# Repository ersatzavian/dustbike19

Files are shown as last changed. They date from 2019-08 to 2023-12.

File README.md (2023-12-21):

# Dustbike 2019

Project to put some custom lights on my crappy playa bike. 

## Key Parts

Part | Manufacturer | Manufacturer Part Number | Qty| Link 
-----|--------------|--------------------------|----|------
Controller | ST Micro | Nucleo-L432KC | 1 | [Digi-Key](https://www.digikey.com/product-detail/en/NUCLEO-L432KC/497-16592-ND/6132763/?itemSeq=297939740)
Color strips | Adafruit | "Dotstar" APA102 strip, 60 LEDs/m, 1m | 2 | [Adafruit](https://www.adafruit.com/product/2239?length=2)
Flood lights | "Lylla" | "Cree U5 LED"... | 1 | [Amazon](https://www.amazon.com/gp/product/B018FM5D0Q/ref=ox_sc_act_title_1?smid=A3W2SO842MQ1IS&psc=1)
Tail light | "Partsam" lol | "2x4.5 Inch Motorcycle LED"... | 1 | [Amazon](https://www.amazon.com/Partsam-4-5inch-Motorcycle-Universal-Running/dp/B01GRO844G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)
Battery | ChromeBattery | zb-12-15 (15 Ah) | 1 | [Walmart](https://www.walmart.com/ip/12v-15ah-sealed-lead-acid-sla-battery-t2-terminals-for-zb-12-15/35451382)
Enclosure - Main Box | Bud Industries | NBF-32016 | 1 | [Amazon](https://www.amazon.com/gp/product/B005UPANU2/ref=ppx_yo_dt_b_asin_title_o01_s00?ie=UTF8&psc=1)  
Enclosure - Control Panel | "Awclub" | 6.2"x3.5"x1.8" | 1 | [Amazon](https://www.amazon.com/gp/product/B07NSV11XR/ref=ppx_yo_dt_b_asin_title_o01_s02?ie=UTF8&psc=1)
Passthrough connectors (RJ45) | "Anmbest" | "Shielded RJ45 Waterproof Cat5/Cat5c"... | 6 | [Amazon](https://www.amazon.com/gp/product/B07KSSV8LD/ref=ppx_yo_dt_b_search_asin_title?ie=UTF8&psc=1)
Solar charger | Renogy | 16W | 1 | [Amazon](https://www.amazon.com/gp/product/B07Q8G3T45/ref=ppx_yo_dt_b_search_asin_title?ie=UTF8&psc=1)
Hall sensor | ZF Electronics | MP101301 | 1 | [Allied Electronics](https://www.alliedelec.com/view/search?keyword=MP101301) 
5V Regulator | Bel Fuse | VRAE-10E1A0G | 1 | [Digi-Key](https://www.digikey.com/product-detail/en/VRAE-10E1A0G/507-1384-ND/1754625/?itemSeq=297936215)
NFETs (Used for Floods, Taillight, Panel voltmeter) | ST Micro | STP40NF03L | 3 | [Digi-Key](https://www.digikey.com/product-detail/en/STP40NF03L/497-3187-5-ND/654529/?itemSeq=301171507)
SSRs (Used to tie charger ground to system ground) | Toshiba Semiconductor | TLP3544(F) | 1 | [Digi-Key](https://www.digikey.com/product-detail/en/TLP3544(F)/TLP3544(F)-ND/3056609/?itemSeq=299990184)
Panel Voltmeter | "DROK" hahaha | "DC 2.7-30V Voltage Tester Meter 5V 9V 12V 24V" | 1 | [Amazon](https://www.amazon.com/DROK-2-7-30V-Digital-Voltmeter-Panel/dp/B07QWKLCX7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)

## Component Prep

### Nucleo Board

* SB9 is populated from the factory with a 0 Ohm jumper, which allows the ST-Link target to control the nRST line on the controller. I cleared this so that the unpowered ST-Link wouldn't be hanging on the nRST line. This may have been unnecessary. 

## Important Pinouts I Probably Shouldn't Forget

I mostly used T568B color/pin number mapping except for the color strips, where I didn't because I was young and foolish. 

Note that the RJ45 passthrough connectors look like they're pinned straight through, but they do actually cross over internally so pin 1 maps to pin 1. 

### Color Strips

Pin | Color | Signal
----|-------|--------
1 | Orange | 5V
2 | Orange/White | 5V
3 | Green/White | 5V
4 | Green | MOSI
5 | Blue/White | SCLK
6 | Blue | GND
7 | Brown/White | GND
8 | Brown | GND

### Floods

Pin | Color | Signal
----|-------|-------
1 | Orange | 12V
2 | Orange/White | 12V
3 | Green/White | 12V
4 | Blue | 12V
5 | Blue/White | Return
6 | Green | Return
7 | Brown/White | Return
8 | Brown | Return

### Control Panel

Pin | Color | Signal
----|-------|--------
1 | Orange/White | Switch 1 (Charge SSR and Panel Meter enable)
2 | Orange | Switch 2 (Color mode enable)
3 | Green/White | Switch 3 (Was wig-wag mode, removed when I found out lights had toggling modes and also burned up one of my NFETs)
4 | Blue | Switch 4 (Floods enable)
5 | Blue/White | Switch 5 (Taillight enable)
6 | Green | Switch 6 (Patrol mode enable)
7 | Brown/White | Pushbutton Switch 7 (was going to be meter enable, then I just tied that to switch 1 because I wanted to use serial debug and collided on pins)
8 | Brown | Ground

### Speed Sensor

Pin | Color | Signal
----|-------|--------
1 | Orange/White | 5V
2 | Orange | NC
3 | Green/White | NC
4 | Blue | NC
5 | Blue/White | NC
6 | Green | Signal (open drain)
7 | Brown/White | NC
8 | Brown | Ground

### Pinouts inside the box 

#### Controller I/O Terminal Block - Left Side 

Pin | Signal
----|--------
1 | SCLK
2 | SCLK
3 | SCLK
4 | MOSI
5 | MOSI
6 | MOSI
7 | SW2 Enable (Taillight Enable output)
8 | SSR1 Enable (Charge / Panel Meter enable)
9 | SW1 Enable (Left Flood enable, til I blew it up and put them together on SW3)
10 | SW3 Enable (Right Flood enable, then both)

#### Controller I/O Terminal Block - Right Side

Pin | Signal 
----|-------
1 | Speed In
2 | CTRL1
3 | CTRL2
4 | CTRL3
5 | CTRL4
6 | CTRL5
7 | CTRL6
8 | CTRL7
9 | SW4 Enable (Meter Enable, til I moved it I think)
10 | GND

## Images

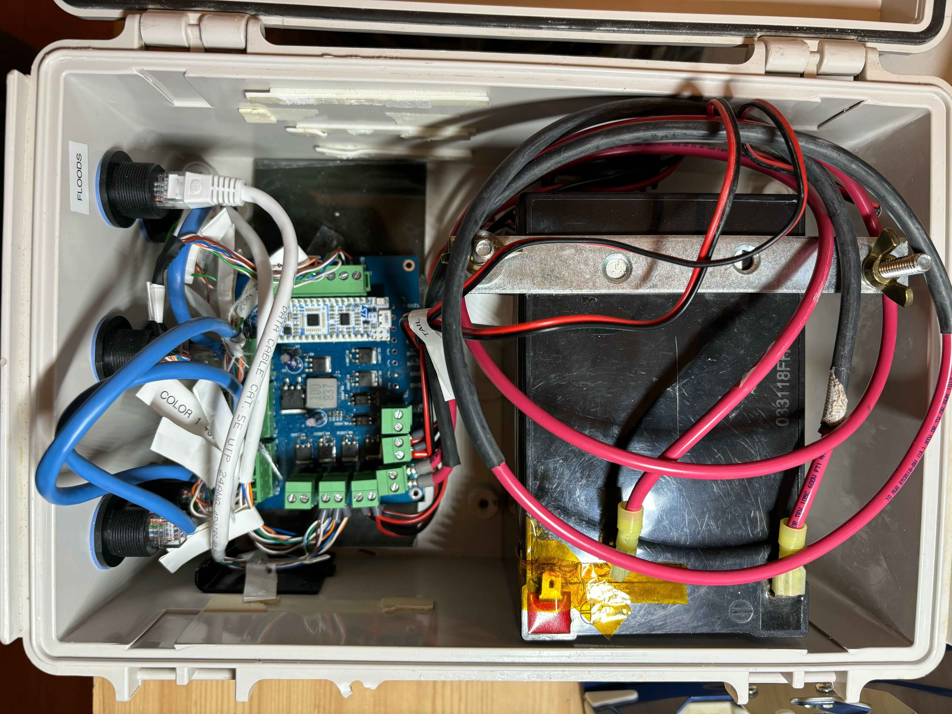
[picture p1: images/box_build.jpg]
Box internals

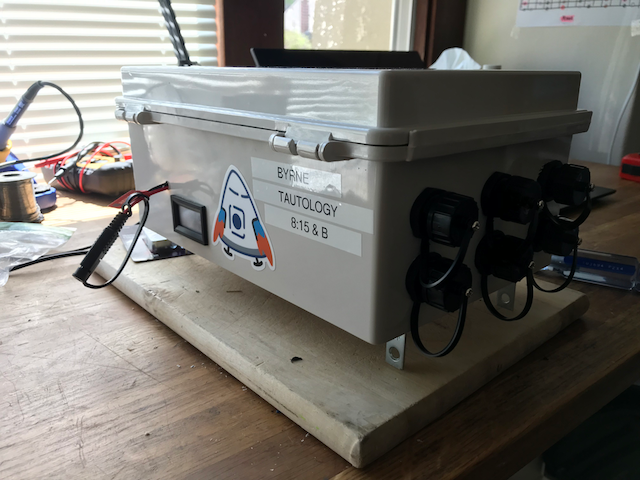
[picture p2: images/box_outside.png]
Box outside

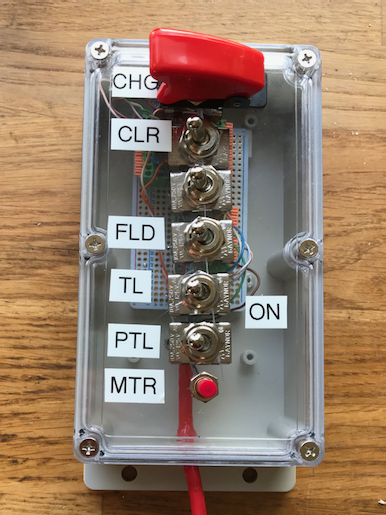
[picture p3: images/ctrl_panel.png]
Control Panel

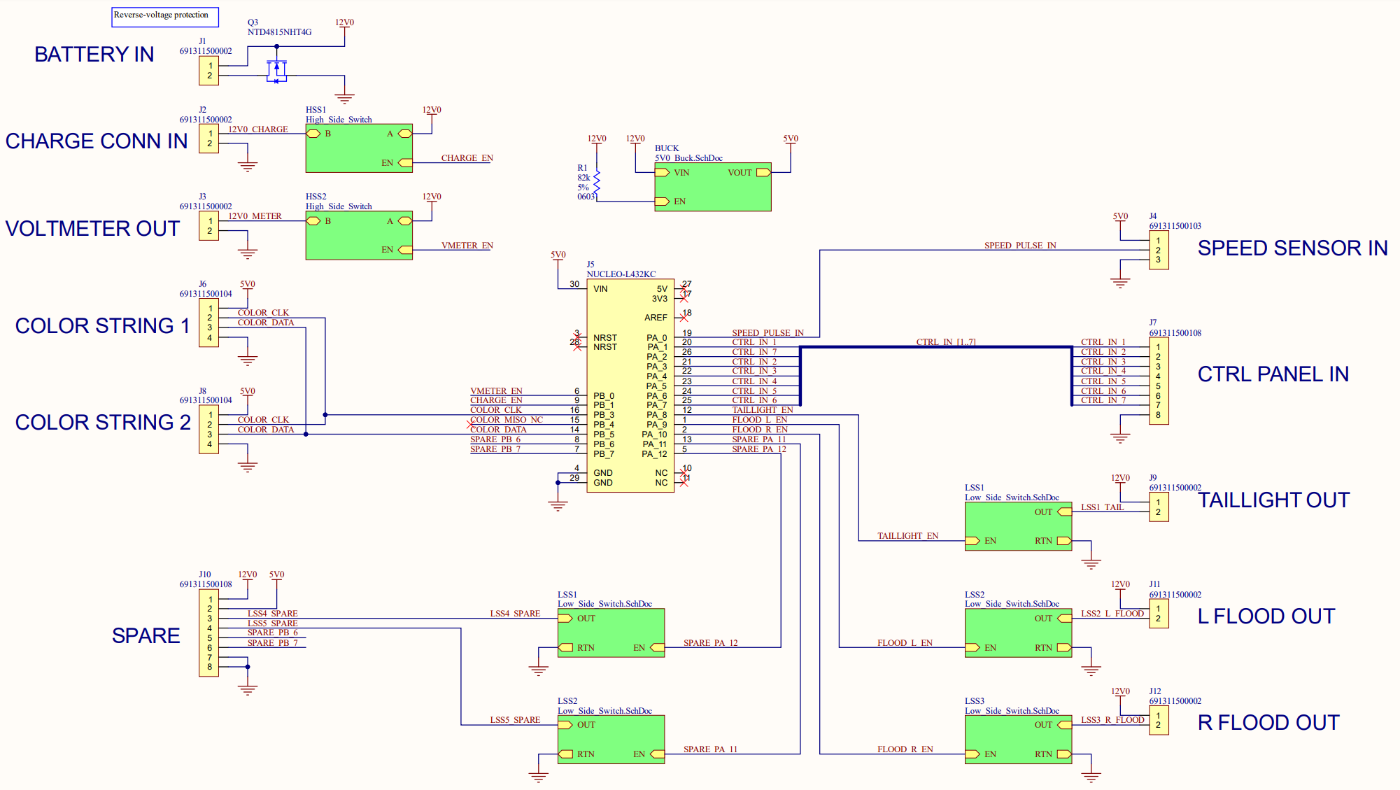
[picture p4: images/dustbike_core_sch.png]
Schematic


Operating in Color mode with floods on: [YouTube](https://youtu.be/-PT2Iv_JQ2k)

Operating in Patrol mode with taillight on: [YouTube](https://youtu.be/xmnZ-JuauxY)

## Issues

Description | Workaround | Fix | Done? 
------------|------------|-----|------
Hall sensor doesn't work with the one MSR bike magnet Tip Top bikes in Oakland Stocks | Use a couple refrigerator magnets I had. | Source a sensor that detects North poles | 
Motorcycle flood lights have three modes and cycle through them on each power cycle (bright, dim, flash rapidly). | It's a feature. | Mod the lights or source some others |
Light pattern speed does not appear to match vehicle speed very well, if at all. | Whatever, it works. | Going to need some test fixturing or at least a test rider. |
Light pattern speed does not update smoothly, especially at low speed. | Whatever, it works. | Add more magnets, or an encoder! |
5V Supply gets quite hot, even at very low load. | Didn't break, doesn't matter. | Design a real board and replace reg. | 
Internal harnessing is a nightmare. | Whatever, it works. | Design a real board. Harness from inside of sealed passthrough connectors straight to board - no terminal blocks. | Yes, see [Dustbike Core](https://github.com/ersatzavian/dustbike19/tree/master/core_hardware/Dustbike_Core)
Using same connector for 12V floods and 5V APA102 strings, as well as control panel and hall sensor. Swapping cables is more likely to be catastrophic than not. | Painted connectors and matching cables matching colors with some of Meb's nail polish. Still did it wrong once and had to replace stuff. | Use different connectors (something compatible with APA102 strings out of the box would be even nicer). |

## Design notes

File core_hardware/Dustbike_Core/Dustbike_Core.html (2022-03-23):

Altium customize

# Board Information Report

Date: | | 3/23/2022
Time: | | 11:38:34 AM
Elapsed Time: | | 00:00:00
Filename: | | C:\Users\TomByrne\dustbike19\core_hardware\Dustbike_Core\Dustbike_Core.PcbDoc
Units: | | mmmils

## Contents

Contents

Board Specification

General

## Board Specification

General
Board Size | 79.756mm x 109.982mm
Components on board | 41

Back to top

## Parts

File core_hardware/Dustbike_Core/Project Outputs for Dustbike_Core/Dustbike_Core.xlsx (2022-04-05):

Description | Designator | Quantity | Manufacturer 1 | Manufacturer Part Number 1 | Supplier 1 | Supplier Part Number 1
CAP CER 1000PF 50V X7R 0603 | C1 | 1 | Samsung Electro-Mechanics | CL10B102KB8NNNC | Digi-Key | 1276-1018-1-ND
CAP ALUM 47UF 20% 25V RADIAL | C2 | 1 | KEMET | ESK476M025AC3FA | Digi-Key | 399-ESK476M025AC3FACT-ND
CAP ALUM 10UF 20% 25V RADIAL | C3 | 1 | Panasonic Electronic Components | ECA-1EM100B | Digi-Key | P19522CT-ND
CAP CER 0.1UF 25V X5R 0603 | C4 | 1 | Samsung Electro-Mechanics | CL10A104KA8NNNC | Digi-Key | 1276-1857-1-ND
DIODE SCHOTTKY 45V 50A D2PAK | D1 | 1 | STMicroelectronics | STPS5045SG-TR | Digi-Key | 497-13279-1-ND
TERM BLOCK HDR 2POS VERT 5.08MM | J1, J2, J3, J9, J11, J12 | 6 | Würth Elektronik | 691311500002 | Digi-Key | 732-2052-ND
TERM BLOCK HDR 3POS VERT 5.08MM | J4 | 1 | Würth Elektronik | 691311500103 | Digi-Key | 732-2059-ND
NUCLEO-32 STM32L432KC EVAL BRD | J5 | 1 | STMicroelectronics | NUCLEO-L432KC | Digi-Key | 497-16592-ND
TERM BLOCK HDR 4POS VERT 5.08MM | J6, J8 | 2 | Würth Elektronik | 691311500104 | Digi-Key | 732-2060-ND
TERM BLOCK HDR 8POS VERT 5.08MM | J7 | 1 | Würth Elektronik | 691311500108 | Digi-Key | 732-2063-ND
FIXED IND 10UH 9A 22 MOHM SMD | L1 | 1 | Sumida America Components Inc. | 125CDMCCDS-100MC | Digi-Key | 308-2561-1-ND
MOSFET P-CH 40V 12A TO252 | Q1 | 1 | Alpha & Omega Semiconductor Inc. | AOD413A | Digi-Key | 785-1218-1-ND
MOSFET N-CH 30V 6.9A/35A DPAK | Q2_LSS3, Q2_LSS11, Q2_LSS12, Q2_LSS21, Q2_LSS22, Q3 | 6 | onsemi | NTD4815NHT4G | Digi-Key | NTD4815NHT4GOSCT-ND
RES 82K OHM 5% 0603 | R1, R4, R7_LSS3, R7_LSS11, R7_LSS12, R7_LSS21, R7_LSS22 | 7
RES 10 OHM 5% 0603 | R2 | 1
RES 0 OHM JUMPER 1/10W 0603 | R3 | 1 | Stackpole Electronics Inc | RMCF0603ZT0R00 | Digi-Key | RMCF0603ZT0R00TR-ND
RES 2.7K OHM 5% 0603 | R5 | 1
RES 20K OHM 5% 0603 | R6 | 1
RES 100 OHM 5% 0603 | R8_HSS1, R8_HSS2 | 2
PWM/VFM STEP-DOWN DCDC CONTROLLE | U1 | 1 | Nisshinbo Micro Devices Inc. | R1224N102M-TR-FE | Digi-Key | 2129-R1224N102M-TR-FECT-ND
SSR RELAY SPST-NO 2A 0-40V | U2_HSS1, U2_HSS2 | 2 | Toshiba Semiconductor and Storage | TLP241AF(TP4,F | Digi-Key | TLP241AF(TP4FCT-ND

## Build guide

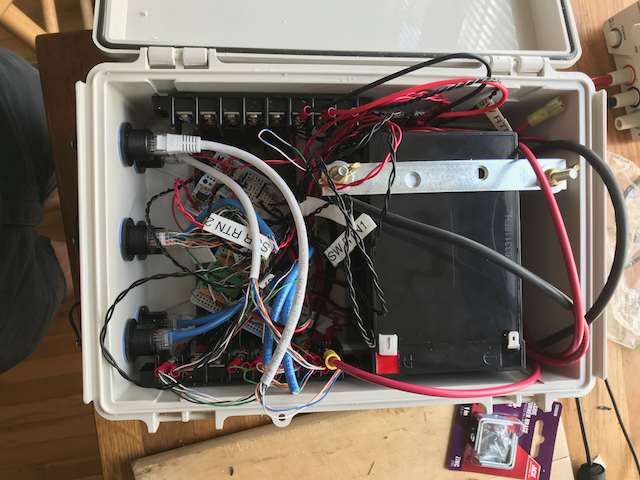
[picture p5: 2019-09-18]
images/box_build.png

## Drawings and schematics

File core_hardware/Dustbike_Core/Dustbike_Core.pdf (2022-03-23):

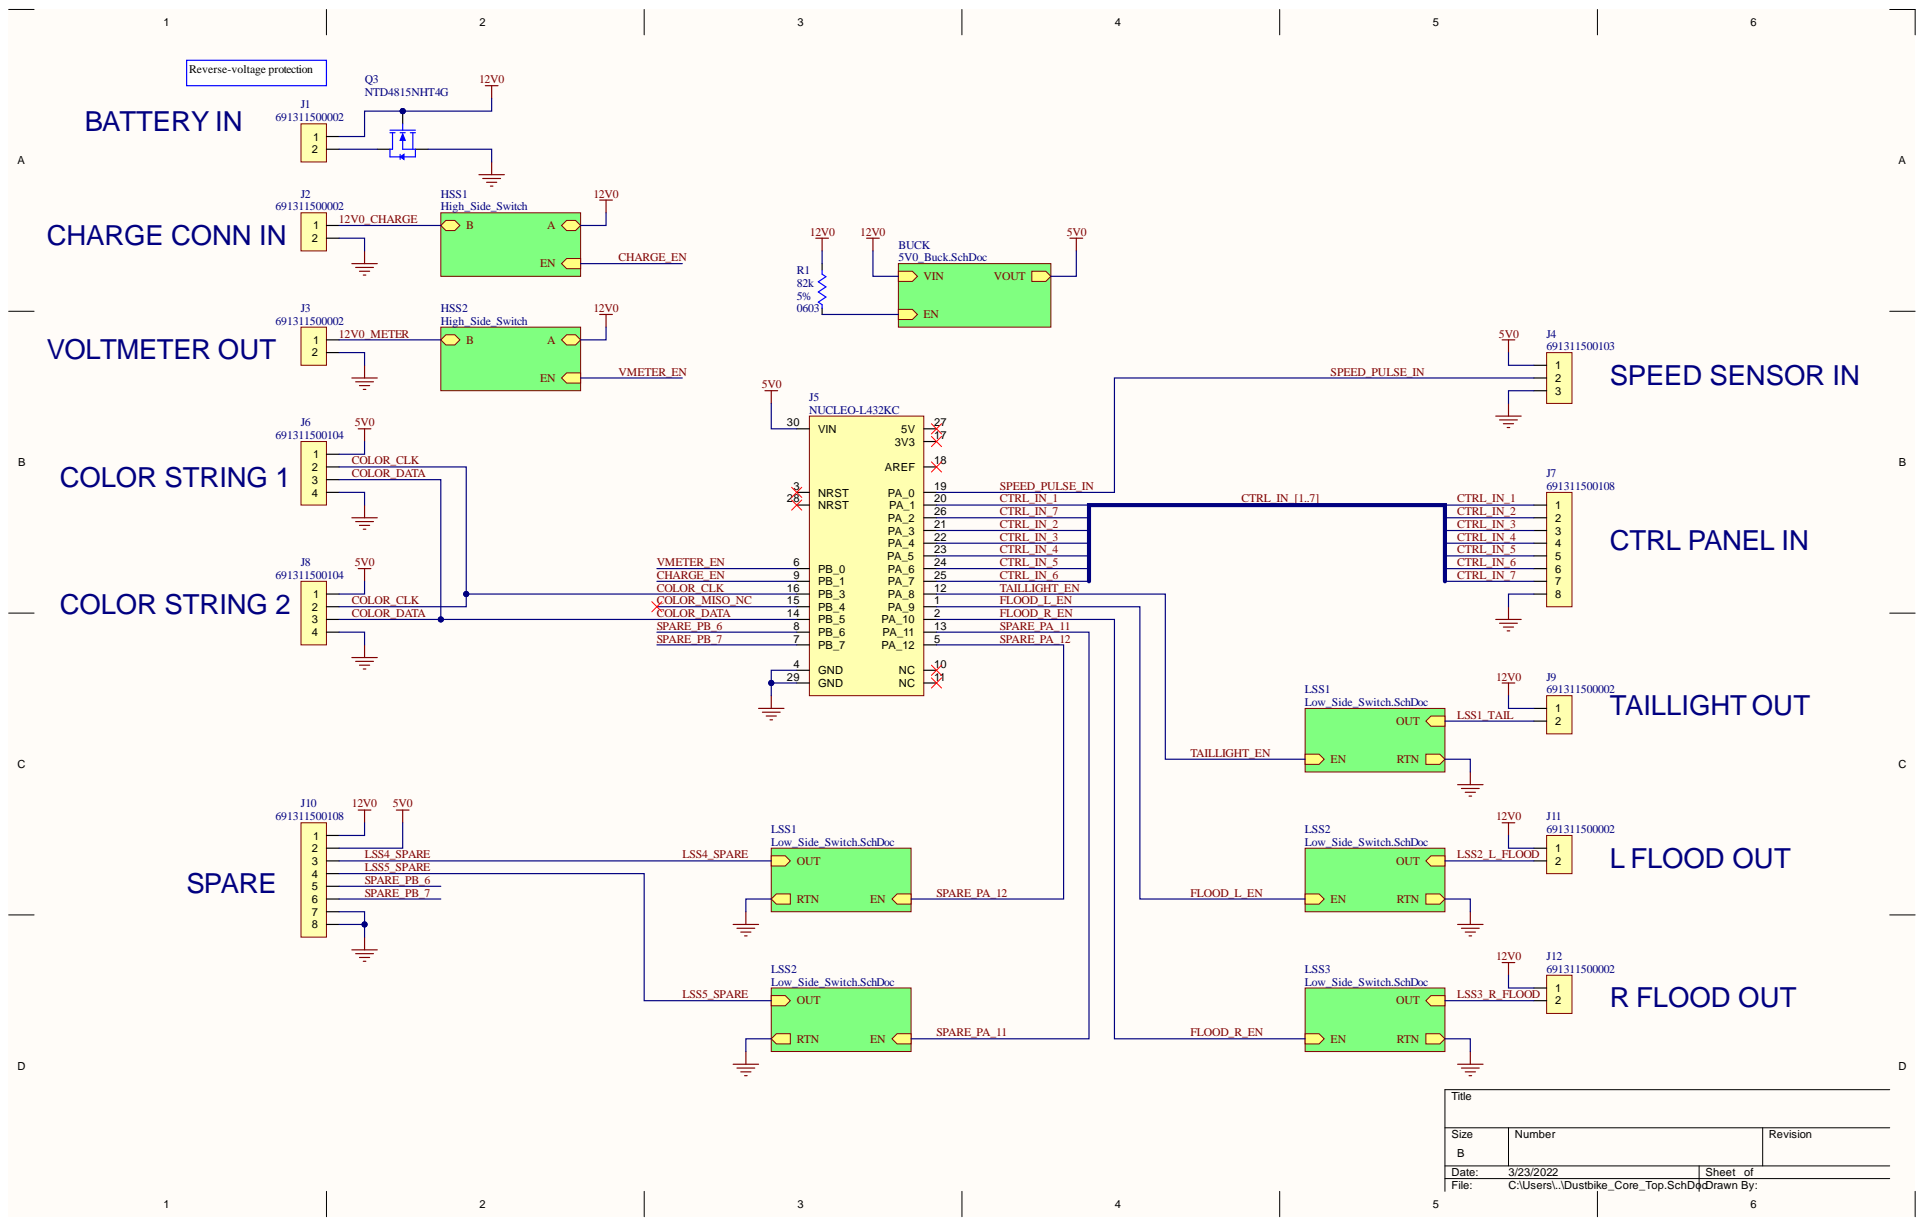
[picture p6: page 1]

SPARE_PA_12 | | FLOOD_L_EN

SPARE_PA_11 | FLOOD_R_EN

Size B | Number | Revision

Date: 3/23/2022 | Sheet of
File: C:\Users\..\Dustbike_Core_Top.SchDocDrawn By:

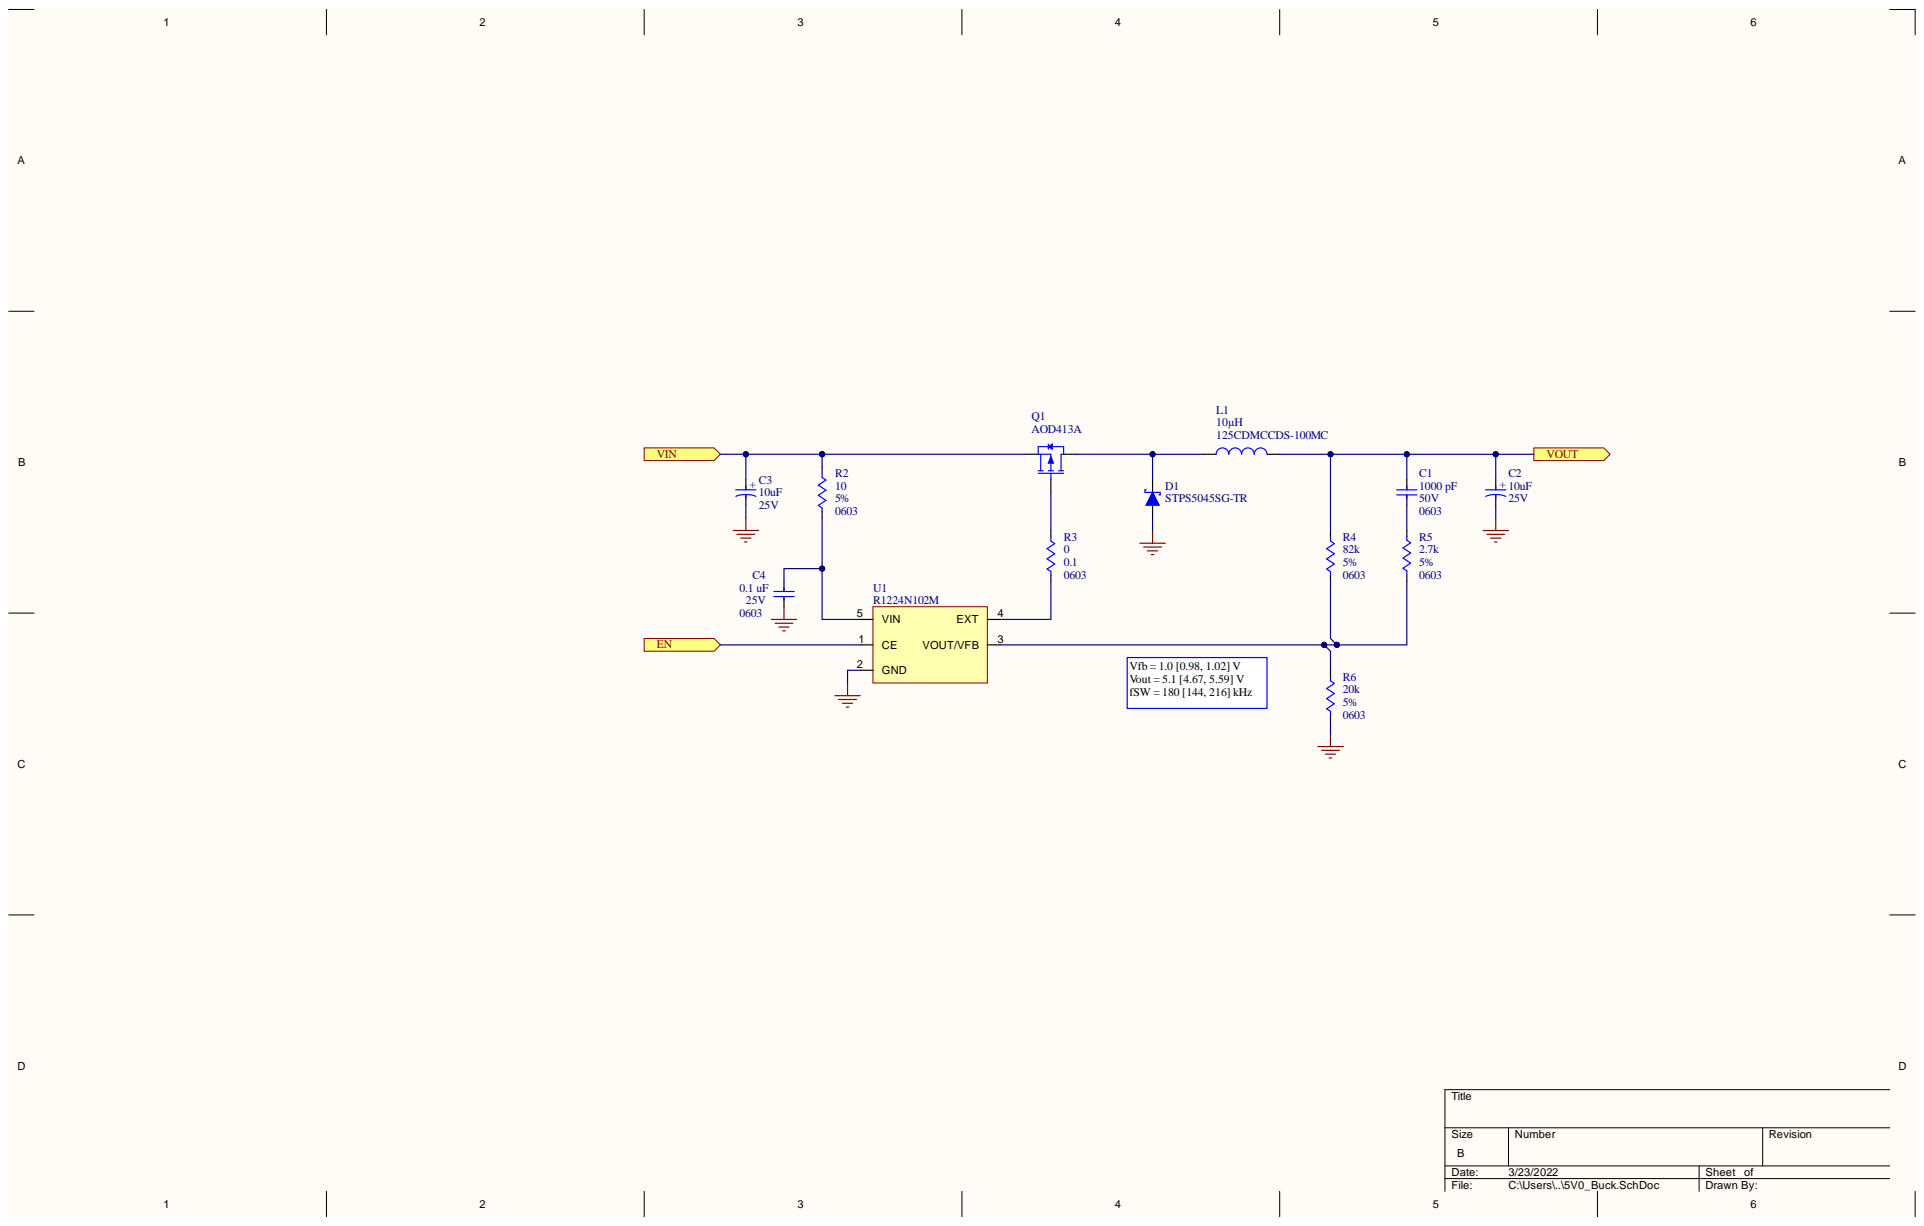
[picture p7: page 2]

S i z e | N umb e r | R e v i s i o n

t e : 3 /2 3 /2 0 2 2 | S h e e t o f
F i l e : C : \ U s e r s \ . . \ 5 V 0 _ B u c k . S c h D o c | D r a w n B y :

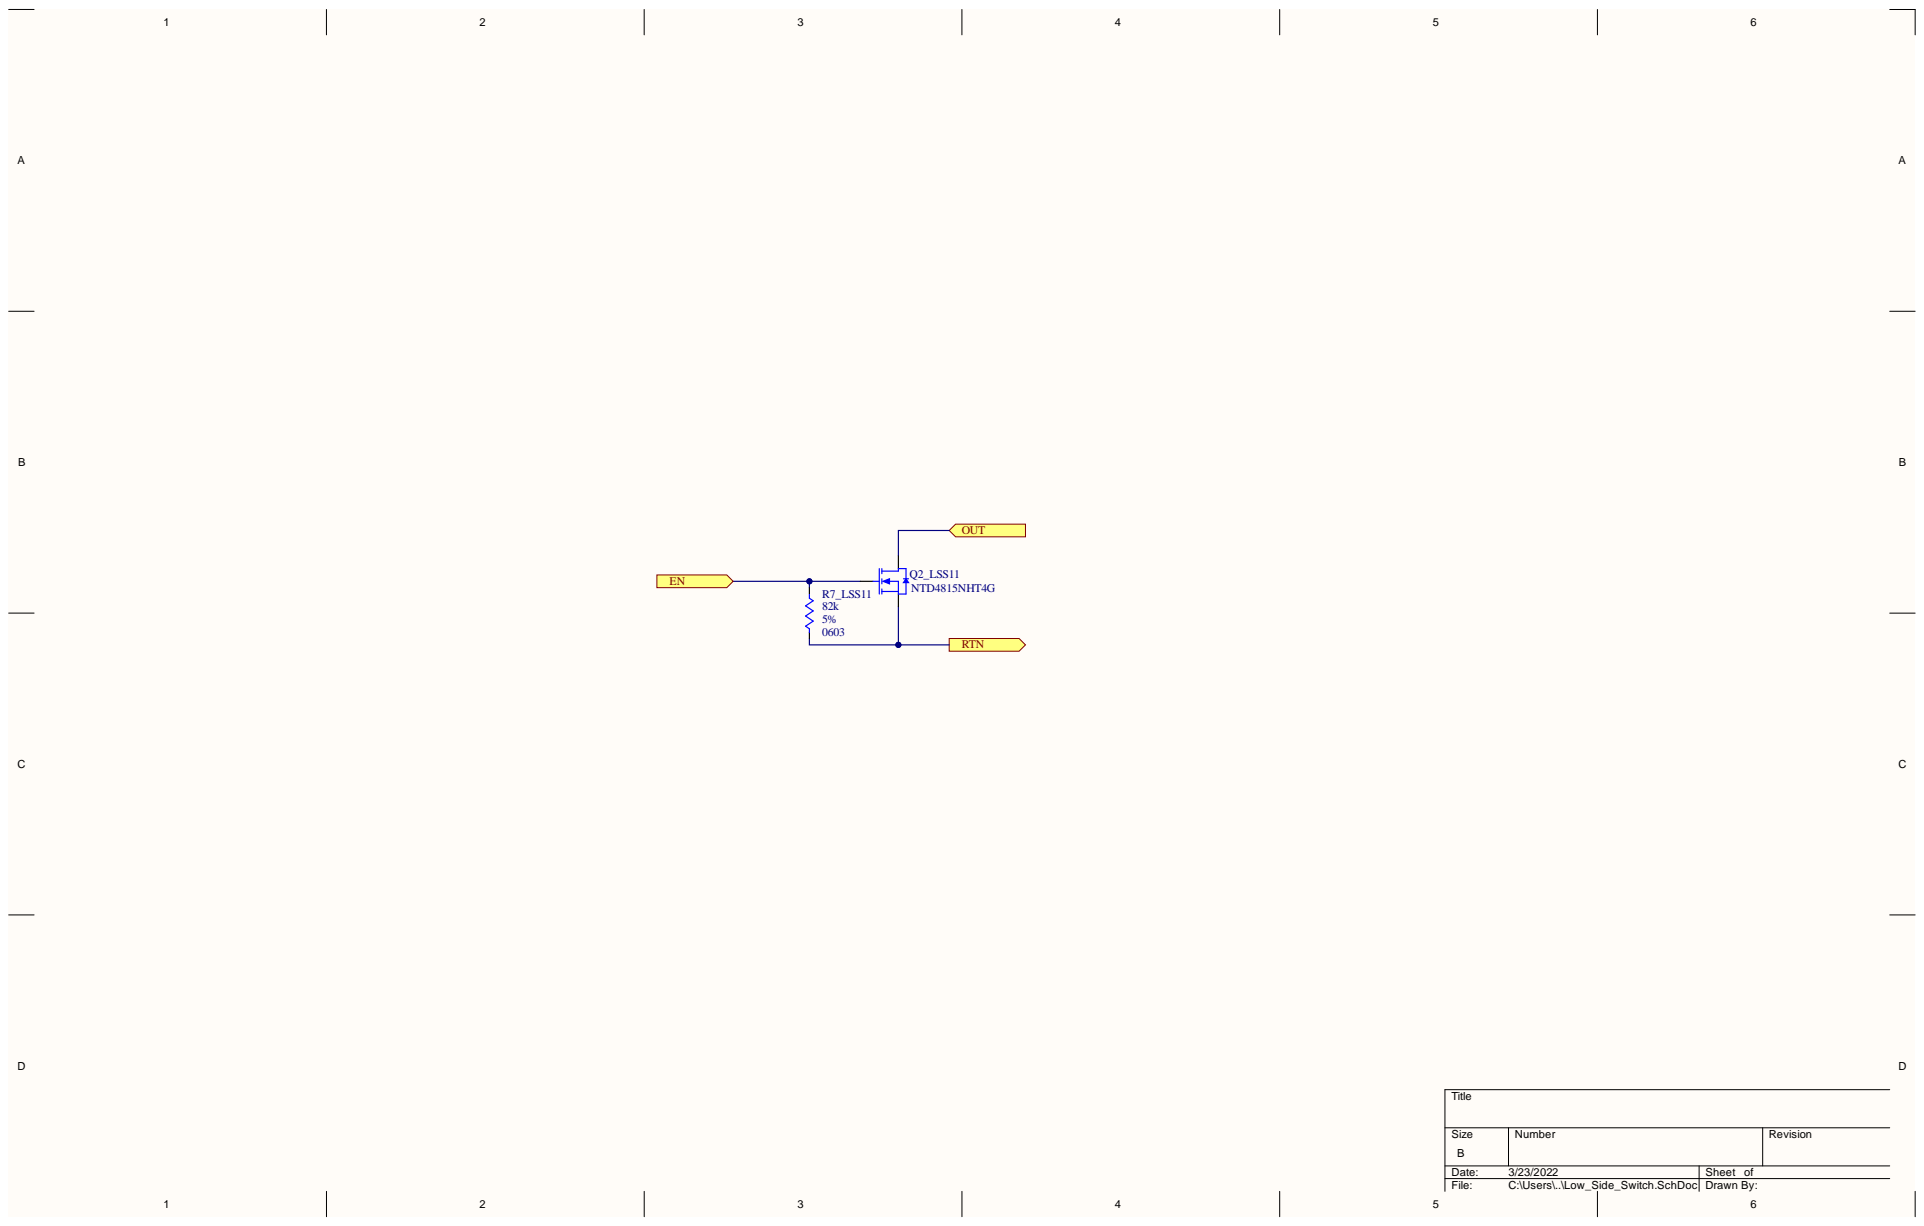
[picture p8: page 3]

S i z e | N umb e r | R e v i s i o n

t e : 3 /2 3 /2 0 2 2 | S h e e t o f
F i l e : C : \ U s e r s \ . . \ L o w _ S i d e _ S w i t c h . S c h D o c | D r a w n B y :

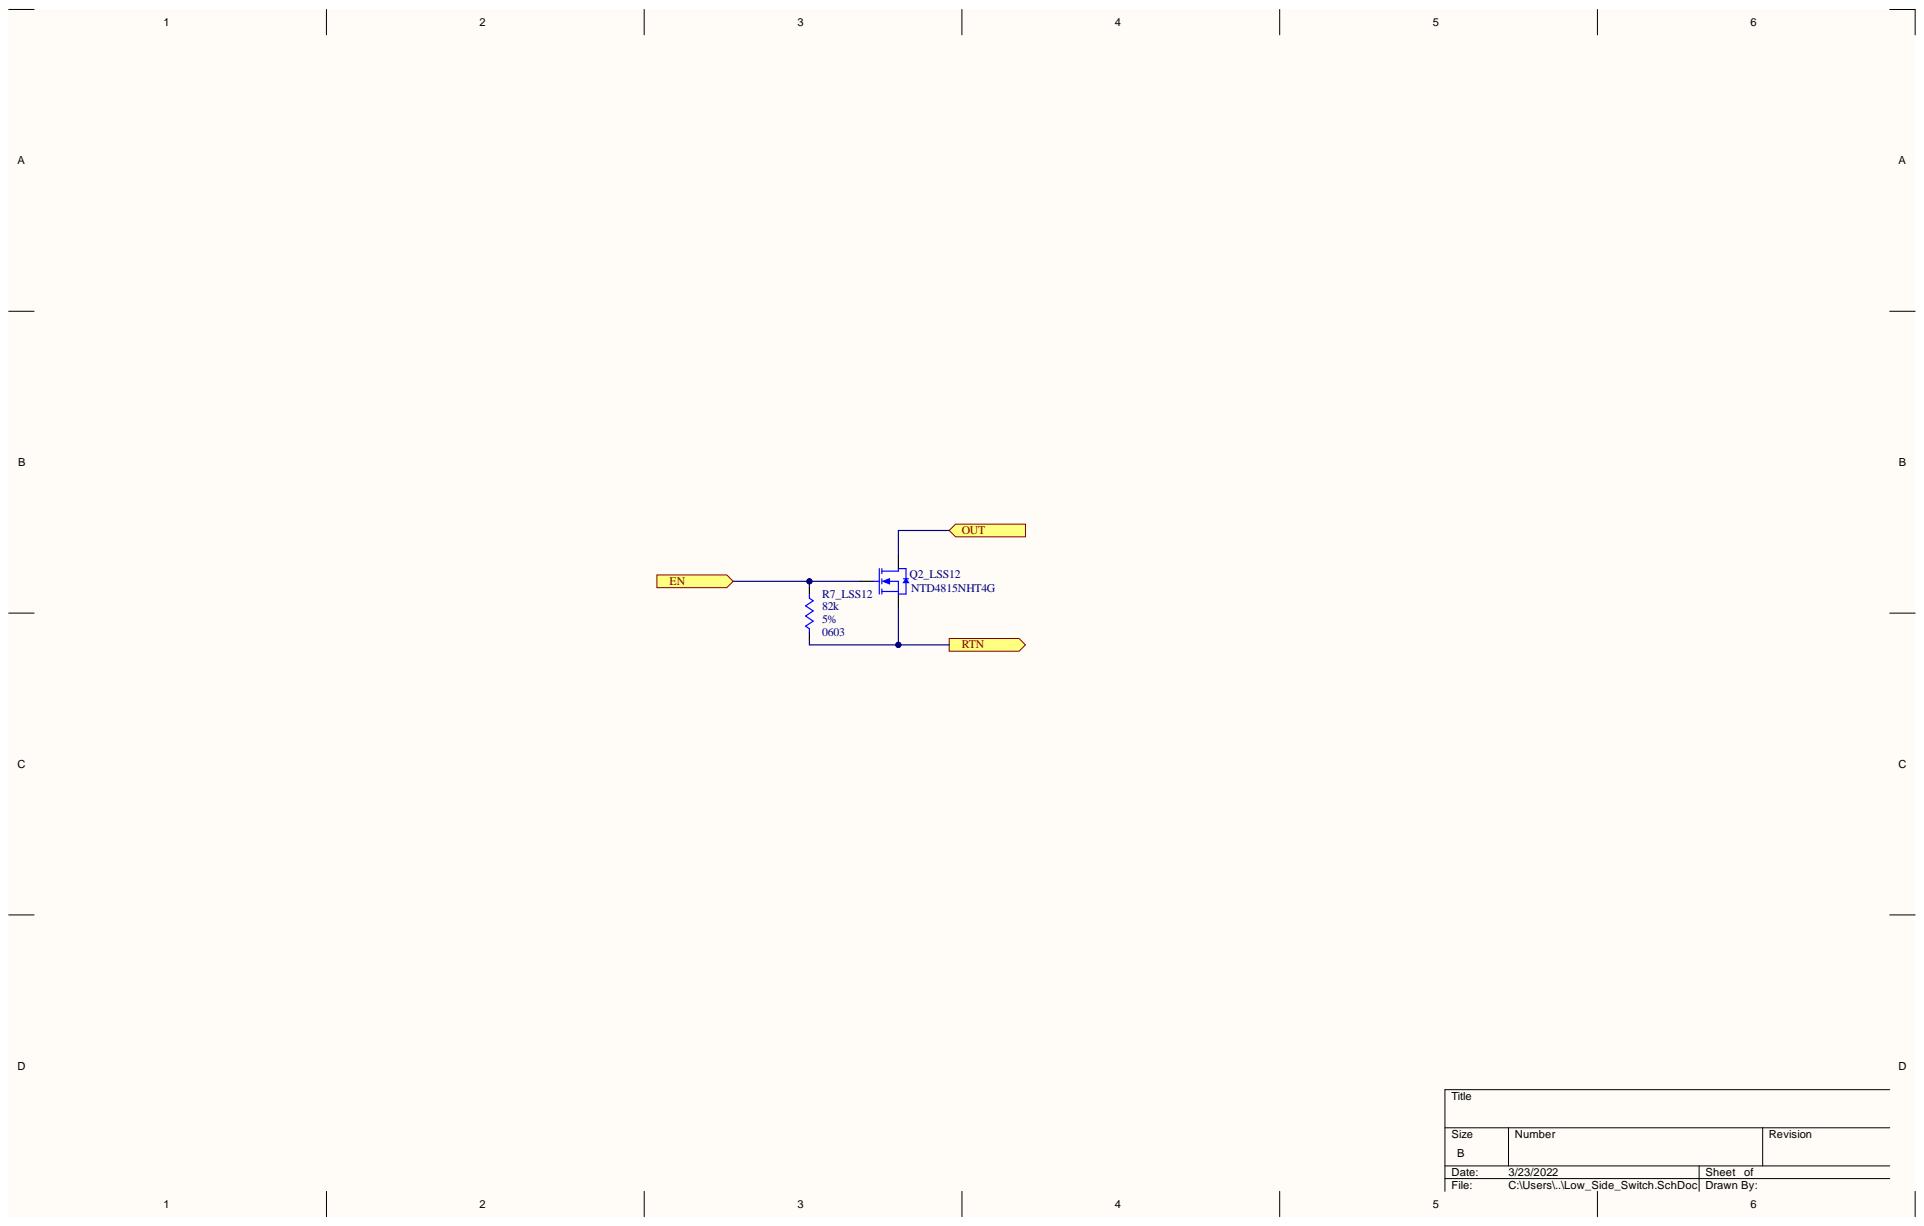
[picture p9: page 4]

Size B | Number | Revision

Date: 3/23/2022 | Sheet of
File: C:\Users\..\Low_Side_Switch.SchDoc | Drawn By:

S i z e | N umb e r | R e v i s i o n

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

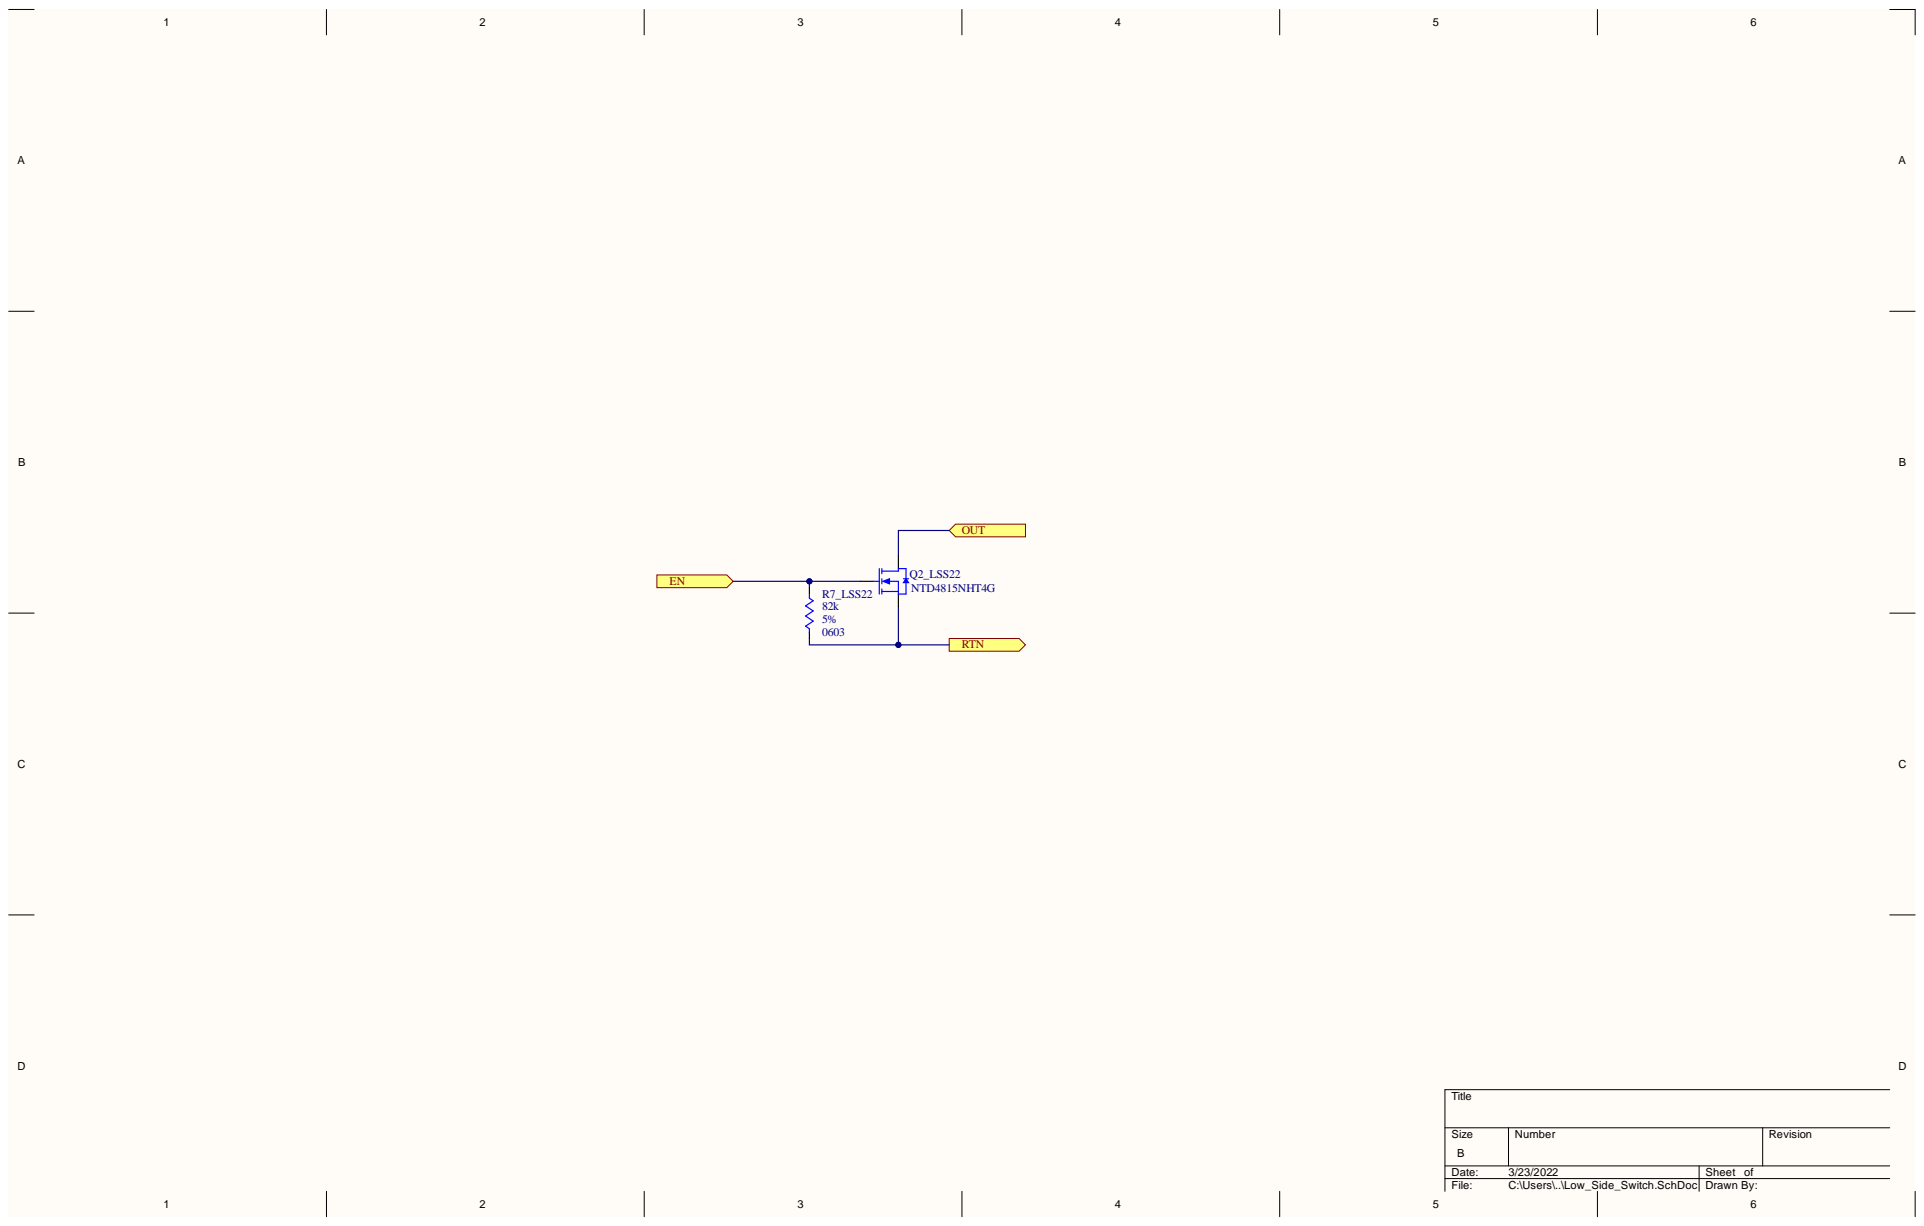
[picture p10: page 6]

Size B | Number | Revision

Date: 3/23/2022 | Sheet of
File: C:\Users\..\Low_Side_Switch.SchDoc | Drawn By:

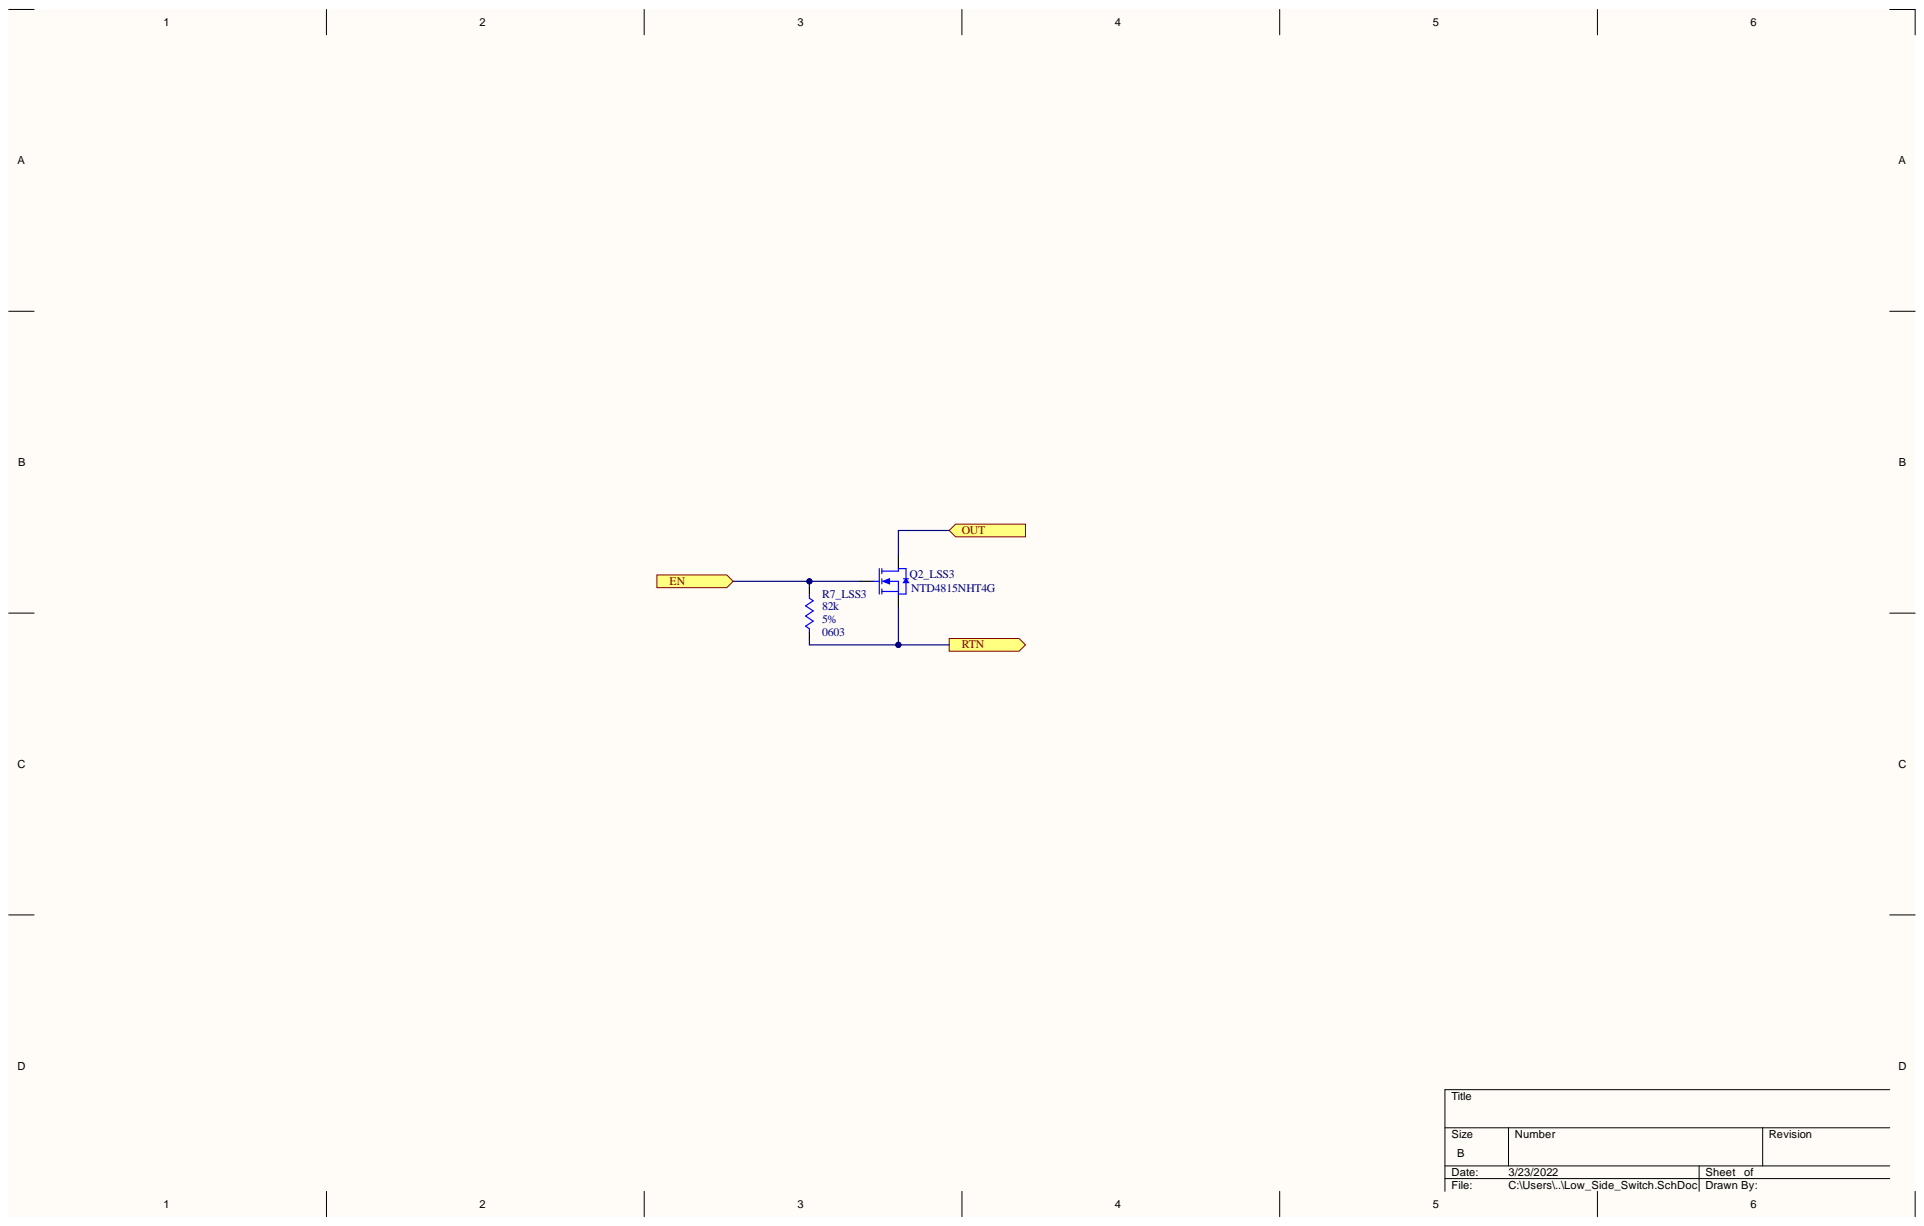
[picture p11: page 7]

S i z e | N umb e r | R e v i s i o n

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

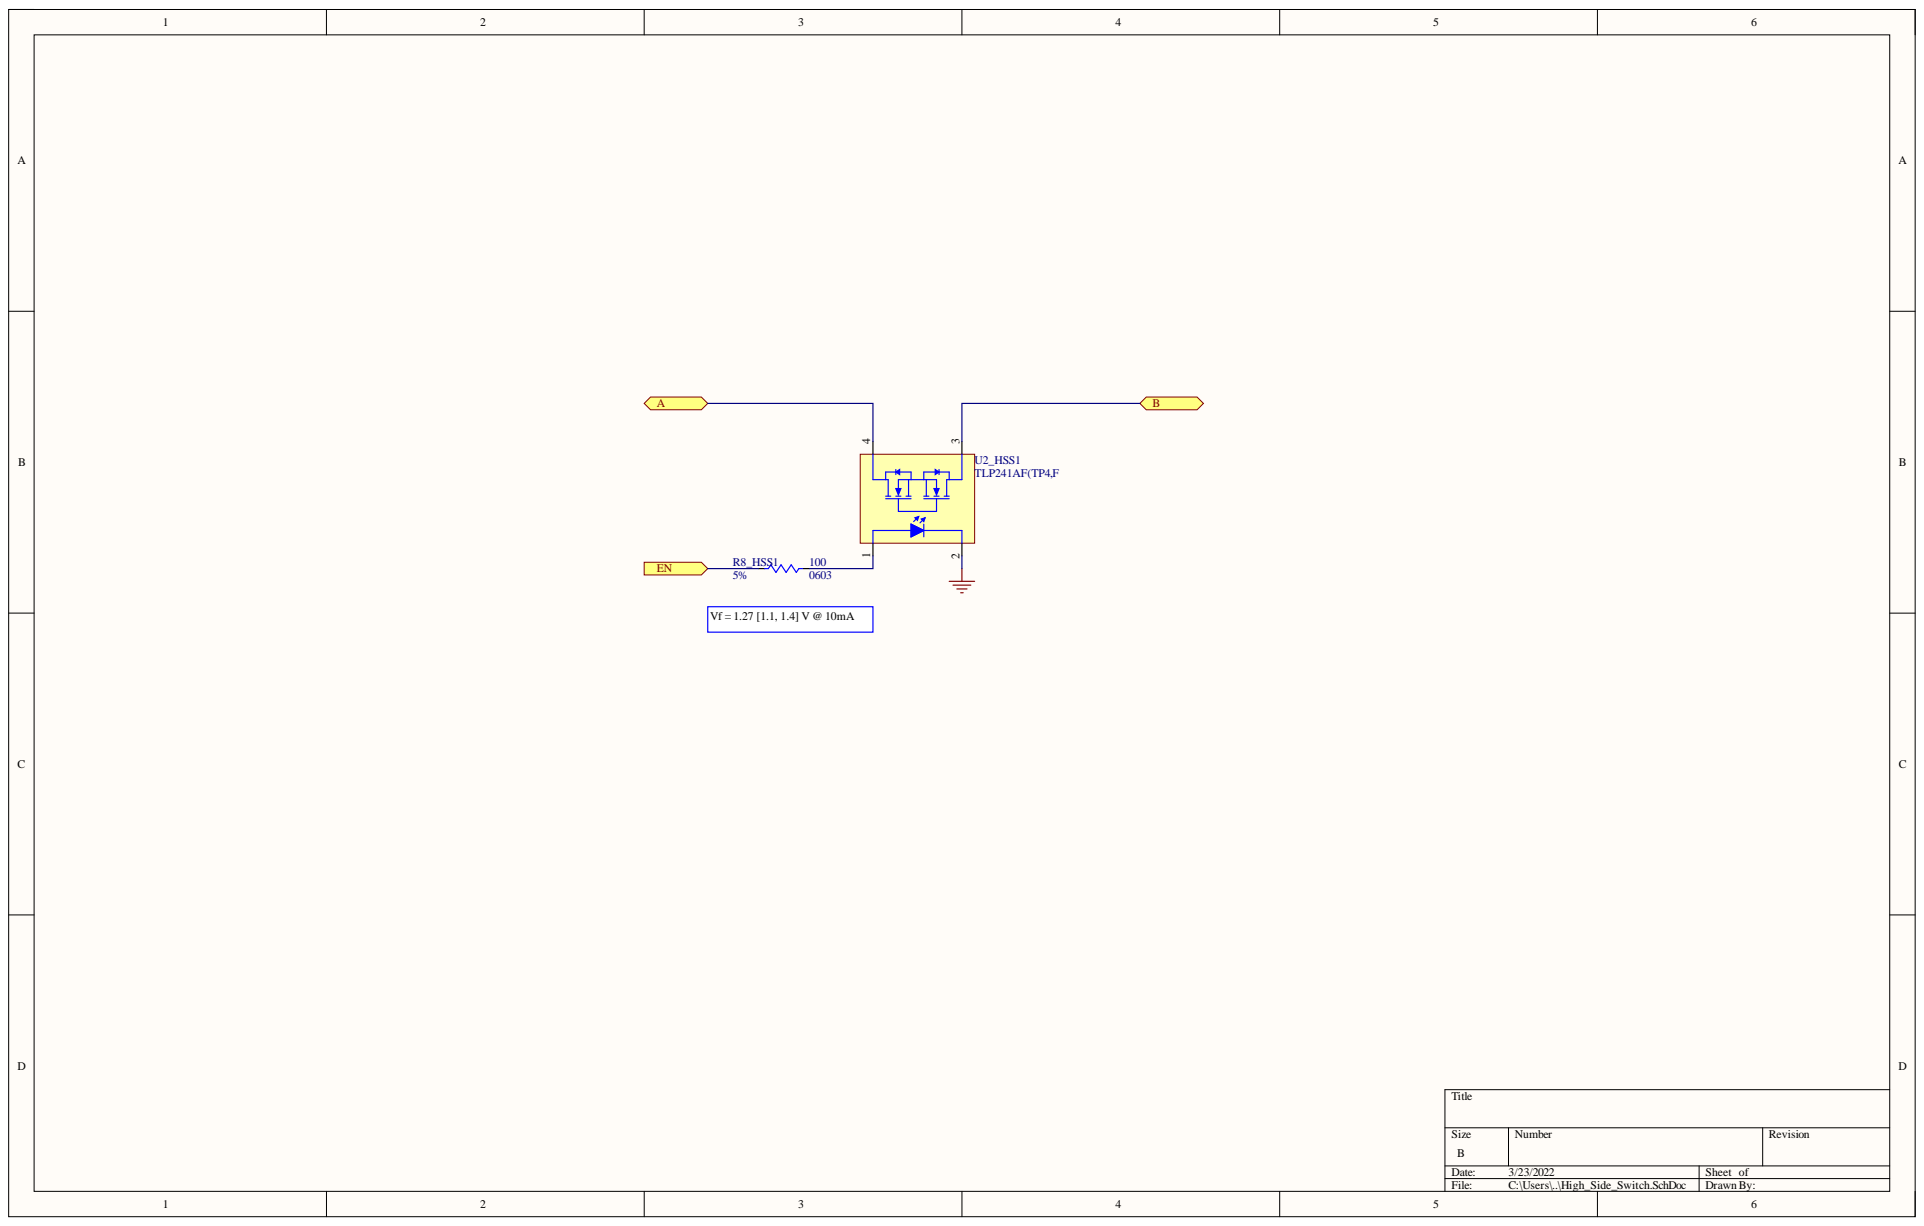
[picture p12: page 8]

Size B | Number | Revision

Date: 3/23/2022 | Sheet of
File: C:\Users\..\High_Side_Switch.SchDoc | Drawn By:

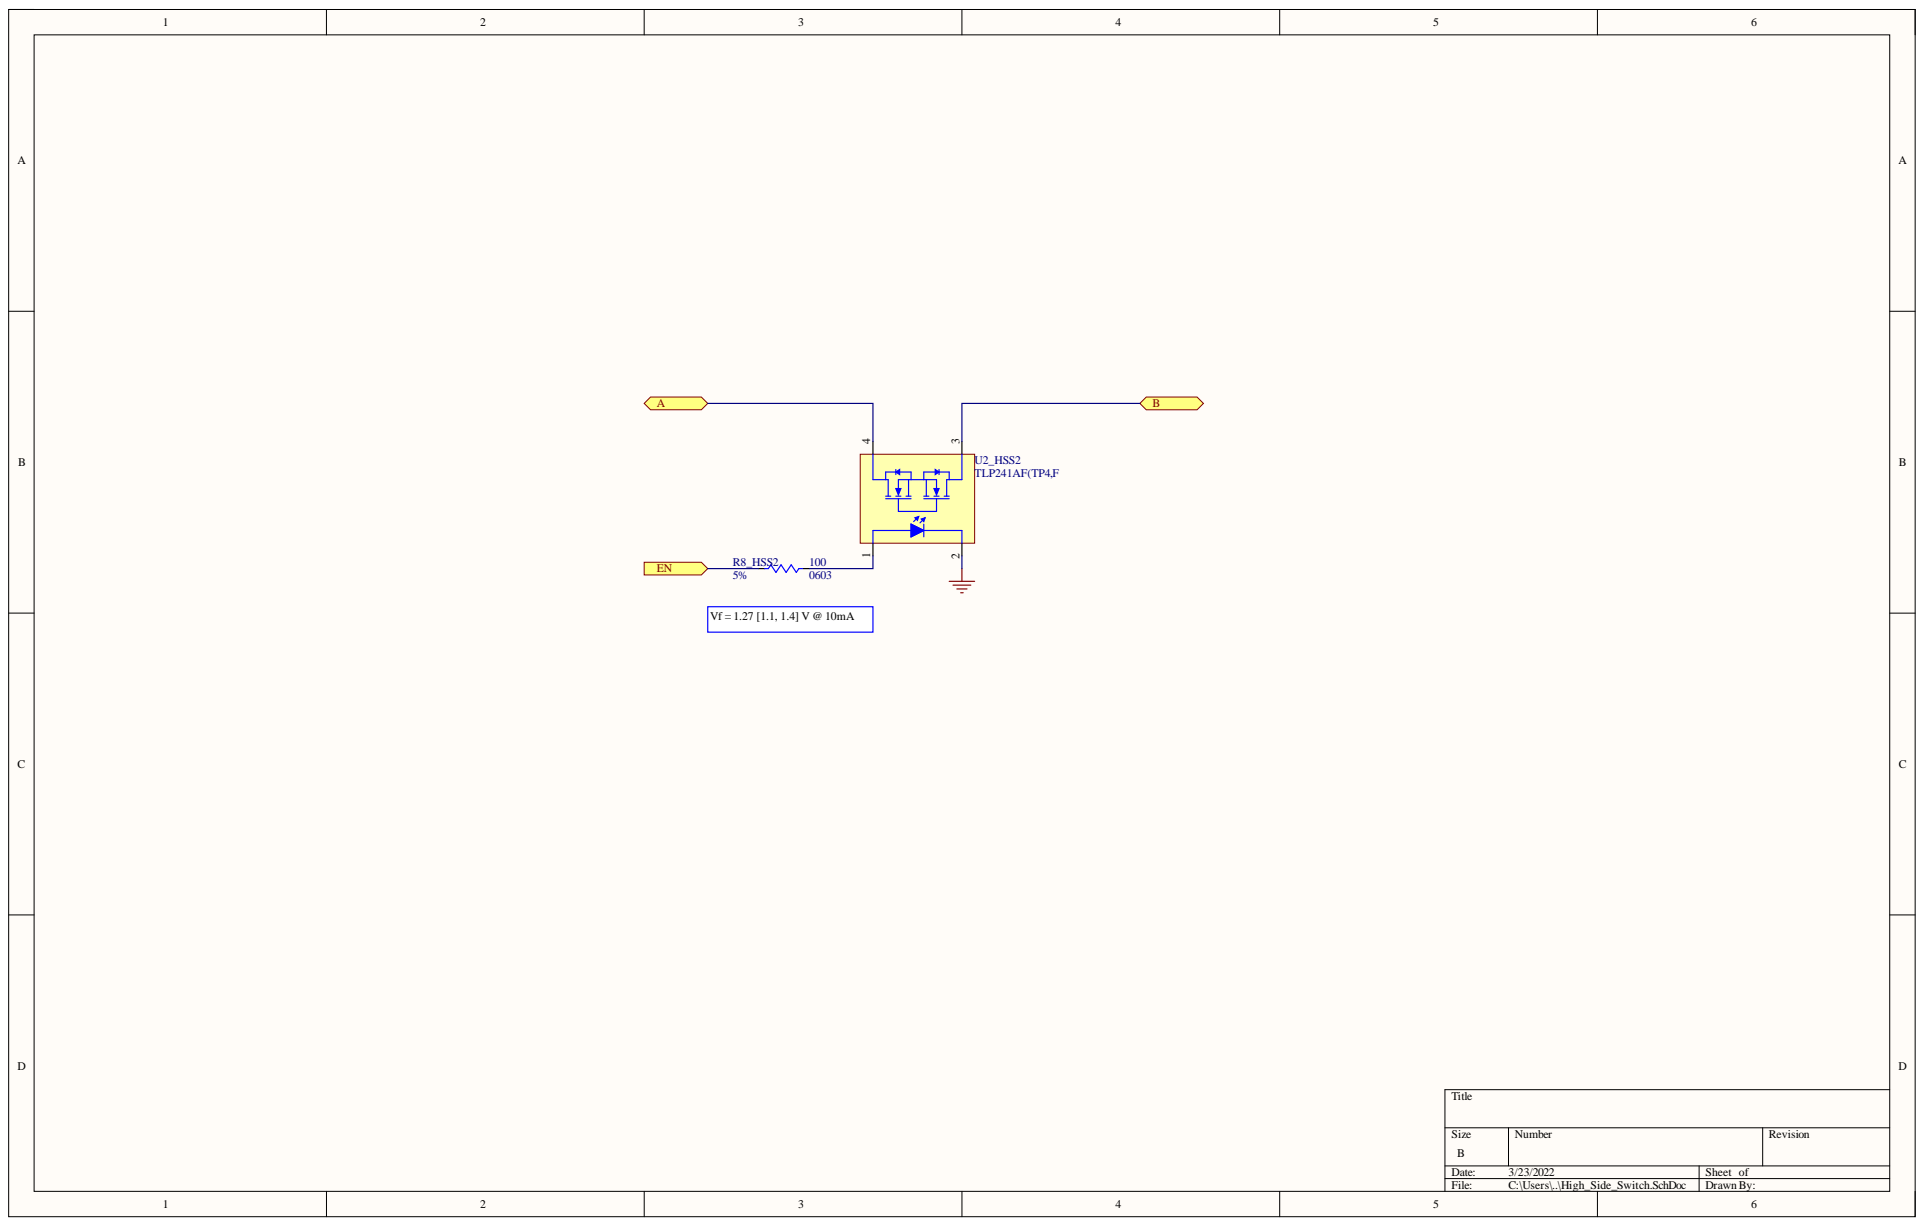
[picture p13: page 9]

Size B | Number | Revision

Date: 3/23/2022 | Sheet of
File: C:\Users\..\High_Side_Switch.SchDoc | Drawn By:

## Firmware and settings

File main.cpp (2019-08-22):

/* mbed Microcontroller Library
 * Copyright (c) 2018 ARM Limited
 * SPDX-License-Identifier: Apache-2.0
 */

#include "mbed.h"

//#define SERIALTEST

#define UPDATE_PERIOD_MS            100 // (msec)
#define APA102_COUNT                64
#define APA102_LEVEL                31 // brightness 0-31
#define SPI_RATE_HZ                 500000  
#define PWM_RATE_HZ                 500
#define WHEEL_CIRC_MM               2170.0 // wheel circumference in millimeters.
#define NUM_WHEEL_MAGNETS           2 // number of evenly-spaced speed sensor magnets
#define PIXELS_PER_METER            60.0
#define FULL_SPEED_MPS              6.7 // about 15 mph; set the taillight on full at this speed.
#define MAX_SPEED_MPS               18.0 // about 40 mph; used to debounce the mag switch
#define TEST_TIME_SINCE_WHEELTICK_US     2000000 // 100 ms/tick * 4 ticks/rev * 1 rev/2.17m = 0.184 s/m = 5.4 m/s = 12mph
#define WIG_WAG_RATE_S              1.0
#define PATROL_COLOR_RATE_S         0.4
#define MIN_TIME_BETWEEN_TICKS_US  (WHEEL_CIRC_MM * 1000)/ (NUM_WHEEL_MAGNETS * MAX_SPEED_MPS)

/* Pin assignments */ 
#define CLK_PIN                 PB_3  // D13
#define DATA_PIN                PB_5  // D11
#define MISO_UNUSED_PIN         PB_4  // D12
#define TAILLIGHT_EN_PIN        PA_8  // D9
#define FLOOD_L_EN_PIN          PA_9  // D1
#define FLOOD_R_EN_PIN          PA_10 // D0
#define CHG_EN_PIN              PB_1  // D6
#define SPEED_IN_PIN            PA_0  // A0
#define METER_EN_PIN            PB_0  // D3
#define CTRL_1_PIN              PA_1  // A1
#define CTRL_2_PIN              PA_3  // A2
#define CTRL_3_PIN              PA_4  // A3
#define CTRL_4_PIN              PA_5  // A4
#define CTRL_5_PIN              PA_6  // A5
#define CTRL_6_PIN              PA_7  // A6
#define CTRL_7_PIN              PA_2  // A7
// virtual com port collides with control 7 (used for panel meter enable)
// PA2 = TX from MCU
// PA15 = RX to MCU
#ifdef SERIALTEST
Serial pc(USBTX, USBRX);
#endif 

SPI spi(DATA_PIN, MISO_UNUSED_PIN, CLK_PIN);
DigitalOut taillight(TAILLIGHT_EN_PIN);
// NFET Switches 2-4 have high threshold voltages and have external pullups
// Use DigitalInOut instead of DigitalOut so we can configure Open Drain
DigitalOut floods(FLOOD_R_EN_PIN);
DigitalInOut meter_en(METER_EN_PIN);
DigitalOut chg_en(CHG_EN_PIN, 0);

// Inputs
DigitalIn ctrl1(CTRL_1_PIN, PullUp);
DigitalIn ctrl2(CTRL_2_PIN, PullUp);
DigitalIn ctrl3(CTRL_3_PIN, PullUp);
DigitalIn ctrl4(CTRL_4_PIN, PullUp);
DigitalIn ctrl5(CTRL_5_PIN, PullUp);
DigitalIn ctrl6(CTRL_6_PIN, PullUp);
#ifndef SERIALTEST
DigitalIn ctrl7(CTRL_7_PIN, PullUp);
#endif

InterruptIn spd(SPEED_IN_PIN, PullUp);

float time_since_wheeltick = TEST_TIME_SINCE_WHEELTICK_US;

Ticker tick_250us;
Ticker tick_100ms;
Timer t;

int count_250us_colors = 0;
int count_100ms_patrol = 0;
int count_100ms_wigwag = 0;

float speed_mps = 0;

bool colors_active = false;
bool floods_active = false;
bool wig_wag_active = false;
bool patrol_mode_active = false;

// int color_buffer[] = {0x2a034d,0x27054f,0x250851,0x220b53,0x200e55,0x1d1157,
//                       0x1b1459,0x18175b,0x16195d,0x131c5f,0x111f61,0x0e2263,
//                       0x0c2565,0x092867,0x072b69,0x082b69,0x092867,0x0c2565,
//                       0x0e2263,0x111f61,0x131c5f,0x16195d,0x18175b,0x1b1459,
//                       0x1d1157,0x200e55,0x220b53,0x250851,0x27054f,0x2a034d,
//                       0x2a034d,0x27054f,0x250851,0x220b53,0x200e55,0x1d1157,
//                       0x1b1459,0x18175b,0x16195d,0x131c5f,0x111f61,0x0e2263,
//                       0x0c2565,0x092867,0x072b69,0x082b69,0x092867,0x0c2565,
//                       0x0e2263,0x111f61,0x131c5f,0x16195d,0x18175b,0x1b1459,
//                       0x1d1157,0x200e55,0x220b53,0x250851,0x27054f,0x2a034d                    
//                     };

int color_buffer[] = {0x32000f,0x2e0020,0x2a0040,0x210064,0x150096,0x0800b4,0x0400c8,0x0000ff, // 8
                      0x0000ff,0x0400c8,0x0800b4,0x150096,0x210064,0x2a0040,0x2e0020,0x32000f, // 16 (first 8 backwards)
                      0x32000f,0x2e0020,0x2a0040,0x210064,0x150096,0x0800b4,0x0400c8,0x0000ff, // 8
                      0x0000ff,0x0400c8,0x0800b4,0x150096,0x210064,0x2a0040,0x2e0020,0x32000f,
                      0x32000f,0x2e0020,0x2a0040,0x210064,0x150096,0x0800b4,0x0400c8,0x0000ff, // 8
                      0x0000ff,0x0400c8,0x0800b4,0x150096,0x210064,0x2a0040,0x2e0020,0x32000f,
                      0x32000f,0x2e0020,0x2a0040,0x210064,0x150096,0x0800b4,0x0400c8,0x0000ff, // 8
                      0x0000ff,0x0400c8,0x0800b4,0x150096,0x210064,0x2a0040,0x2e0020,0x32000f
                    };

int patrol_color_buffer[] = {0xff0000,0xff0000,0xff0000,0xff0000,0xff0000,0xff0000,
                            0xff0000,0xff0000,0xff0000,0xff0000,0xff0000,0xff0000,
                            0xff0000,0xff0000,0xff0000,0xff0000,0xff0000,0xff0000,
                            0xff0000,0xff0000,0x0000ff,0x0000ff,0x0000ff,0x0000ff,
                            0x0000ff,0x0000ff,0x0000ff,0x0000ff,0x0000ff,0x0000ff,
                            0x0000ff,0x0000ff,0x0000ff,0x0000ff,0x0000ff,0x0000ff,
                            0x0000ff,0x0000ff,0x0000ff,0x0000ff,0xff0000,0xff0000,
                            0xff0000,0xff0000,0xff0000,0xff0000,0xff0000,0xff0000,
                            0xff0000,0xff0000,0xff0000,0xff0000,0xff0000,0xff0000,
                            0xff0000,0xff0000,0xff0000,0xff0000,0xff0000,0xff0000
                            };

void color_draw() {
    int i; 

    // start of frame
    for (i = 0; i < 4; i++) {
        spi.write(0);
    }
    // LED buffer
    for (i = 0; i < APA102_COUNT; i++) {
        spi.write((7<<5) | APA102_LEVEL);
        spi.write(color_buffer[i] & 0xff); // B
        spi.write((color_buffer[i] >> 8) & 0xff); // G
        spi.write((color_buffer[i] >> 16) & 0xff); // R
    }
    // end of frame
    for (i = 0; i < 4; i++) {
        spi.write(1);
    }
}

void color_advance() {
    int temp = color_buffer[0];
    for (int x = 0; x < (APA102_COUNT - 1); x++) {
        color_buffer[x] = color_buffer[x + 1];
        color_buffer[APA102_COUNT - 1] = temp;
    }

    // write out the current buffer
    color_draw();
}

void patrol_draw() {
    int i; 

    // start of frame
    for (i = 0; i < 4; i++) {
        spi.write(0);
    }
    // LED buffer
    for (i = 0; i < APA102_COUNT; i++) {
        spi.write((7<<5) | APA102_LEVEL);
        spi.write(patrol_color_buffer[i] & 0xff); // B
        spi.write((patrol_color_buffer[i] >> 8) & 0xff); // G
        spi.write((patrol_color_buffer[i] >> 16) & 0xff); // R
    }
    // end of frame
    for (i = 0; i < 4; i++) {
        spi.write(1);
    }
}

void patrol_color_advance() {
    for (int x = 0; x < (APA102_COUNT - 1); x++) {
        if (patrol_color_buffer[x] == 0xff0000) {
            // swap red to blue
            patrol_color_buffer[x] = 0x0000ff;
        } else {
            // swap anything but red to red
            patrol_color_buffer[x] = 0xff0000;
        }
    }

    // write out the current buffer
    patrol_draw();
}

void color_clear() {
    int i; 

    // start of frame
    for (i = 0; i < 4; i++) {
        spi.write(0);
    }
    // LED buffer
    for (i = 0; i < APA102_COUNT; i++) {
        spi.write((7<<5) | APA102_LEVEL);
        spi.write(0);
        spi.write(0);
        spi.write(0);
    }
    // end of frame
    for (i = 0; i < 4; i++) {
        spi.write(1);
    }
}

void service_ctrl_panel() {
    bool start_wig_wag = false;

    // service control panel
    // 1: Charge Enable
    if (!ctrl1.read()) {
        chg_en.write(1);
    } else {
        chg_en.write(0);
    }
    // 2: colors_active
    if (!ctrl2.read()) {
        colors_active = true;
    } else {
        colors_active = false;
    }

    // 3: Wig Wag (disabled until power board can be corrected)
    // if (!ctrl3.read()) {
    //     wig_wag_active = true;
    // } else {
    //     wig_wag_active = false;
    // }

    // 4: Floods
    if (!ctrl4.read()) {
        floods_active = true; 
    } else {
        floods_active = false;
    } 

    // 5: Taillight
    if (!ctrl5.read()) {  
        taillight.write(1);
    } else {
        taillight.write(0);
    }
    // 6: Patrol mode
    if (!ctrl6.read()) {
        patrol_mode_active = true;
    } else {
        patrol_mode_active = false;
    }
    // 7: Panel Meter Enable
    #ifndef SERIALTEST
    if (!ctrl7.read()) {
        meter_en.write(1);
    } else {
        meter_en.write(0);
    }
    #endif

    // Patrol mode overrides normal color mode
    if (patrol_mode_active) {
        colors_active = false;
    }

    // Wig-wag overrides floods
    // if (wig_wag_active) {
    //     if (start_wig_wag) {
    //         flood_l.write(1);
    //         flood_r.write(0);
    //     }
    // } else {
        if (floods_active) {
            floods.write(1);
            // flood_l.write(1);
            // flood_r.write(1);
        } else {
            floods.write(0);
            // flood_l.write(0);
            // flood_r.write(0);
        }
    // }
}

void callback_spd_pin() {
    // disable IRQ till we're out of here
    spd.disable_irq();

    time_since_wheeltick = t.read_us();
    // debounce the magnetic switch by discarding reads that are too close together to be real
    if (time_since_wheeltick < MIN_TIME_BETWEEN_TICKS_US) {
        spd.enable_irq();
        return;
    }

    // speed in meters per second works out nicely since mm / ms = m/s
    speed_mps = (WHEEL_CIRC_MM / NUM_WHEEL_MAGNETS) / (time_since_wheeltick / 1000.0);
    t.reset();

    spd.enable_irq();
}

void callback_250us() {
    count_250us_colors++;
}

void callback_100ms() {
    count_100ms_patrol++;
    count_100ms_wigwag++;
}

int main()
{
    // configure DigitalInOut pins as open drain ASAP
    #ifndef SERIALTEST 
    meter_en.output();
    meter_en.mode(OpenDrain);
    meter_en.write(0);
    #endif

    // rest of digital outputs
    floods.write(0);
    taillight.write(0);

    // initialize SPI for APA102 interface
    spi.frequency(SPI_RATE_HZ);

    // initialize the lights to on or off
    // patrol mode overrides normal color mode
    // bools are mutually exclusive coming from the control panel reader
    // but let's keep it tidy here anyway
    if (patrol_mode_active) {
        patrol_draw();
    } else if (colors_active) {
        color_draw();
    } else {
        color_clear();
    }

    // start the speed counter timer
    t.start();
    //attach the speed counter callback
    spd.fall(&callback_spd_pin);

    tick_250us.attach_us(&callback_250us, 250);
    tick_100ms.attach(&callback_100ms, 0.1);

    while (true) {
        // read the controls and update taillight brightness
        service_ctrl_panel();

        // the 250us counter drives the advance rate of the pixels
        // here we are counting on colors_active and patrol_mode_active to be mutually exclusive...
        if (count_250us_colors >= (4000.0 * (1.0/PIXELS_PER_METER) / speed_mps)) {
            if (colors_active) {
                color_advance();
            } else if (!patrol_mode_active) {
                // clean up after other modes since this one is the fastest;
                // if nobody else is using the lights, clear them here
                color_clear();
            }
            count_250us_colors = 0;
        }

        // this 100ms counter drives the color change rate in patrol mode 
        if (count_100ms_patrol / 10.0 >= PATROL_COLOR_RATE_S) {
            if (patrol_mode_active) {
                patrol_color_advance();
            } 
            count_100ms_patrol = 0;
        }
        
        // this 100ms counter drives the blink rate of the wigwag
        if (count_100ms_wigwag / 10.0 >= WIG_WAG_RATE_S) {
            // if (wig_wag_active) {
            //     flood_l.write(1 - flood_l.read());
            //     flood_r.write(1 - flood_r.read());
            // } 
            
            count_100ms_wigwag = 0;
        }
    }
}

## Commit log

2019-08-17 reversed direction of color lights, removed taillight brightness modulation
    [main.cpp]
2022-03-18 Created altium project for core board to replace hand-built prototype
    [5V0_Buck.SchDoc, Dustbike_Core.PrjPcb, Dustbike_Core_Top.SchDoc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]
2022-03-19 finished top sheet of dustbike, working on 5V buck
    [Dustbike_Core.PrjPcb, Dustbike_Core_Top.SchDoc, High_Side_Switch.SchDoc]
2022-03-21 adding parts for 5V buck
    [5V0_Buck.SchDoc, Dustbike_Core.PrjPcb]
2022-03-23 finished schematic capture, imported footprints
    [5V0_Buck.SchDoc, Dustbike_Core.PcbDoc, Dustbike_Core.PrjPcb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]
2022-03-23 got all parts imported into PcbDoc
    [5V0_Buck.SchDoc, Dustbike_Core.PcbDoc, Dustbike_Core.PrjPcb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]
2022-03-23 routing complete, DRC clean
    [5V0_Buck.SchDoc, Dustbike_Core.PcbDoc, Dustbike_Core.PrjPcb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]
2022-03-23 cleanup for release
    [5V0_Buck.SchDoc, Dustbike_Core.PcbDoc, Dustbike_Core.PrjPcb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]
2022-03-23 released dustbike core to fab
    [5V0_Buck.SchDoc, Dustbike_Core.PrjPcb, Dustbike_Core.xlsx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]
2022-04-05 generated BOM'
    [Dustbike_Core.xlsx]
2022-04-07 moved floods back to independent switches, built, added binary to repo
